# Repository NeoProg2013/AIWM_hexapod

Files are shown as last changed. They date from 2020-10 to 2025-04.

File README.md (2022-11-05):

# AIWM hexapod (Artificial intelligence walking machine)



## Цикл статей по разработке:

* https://habr.com/ru/post/424867/ – проектирование
* https://habr.com/ru/post/424905/ – сборка
* https://habr.com/ru/post/436748/ – кинематика
* https://habr.com/ru/post/444070/ – ядро передвижения
* https://habr.com/ru/post/448058/ – электроника
* https://habr.com/ru/post/478812/ – проектирование для 3D печати
* https://habr.com/ru/post/111111/ – пластиковый корпус и прикладное ПО
* https://habr.com/ru/post/493304/ – улучшенная математика передвижения
* https://habr.com/ru/post/507762/ – завершение версии 1.00
* https://habr.com/ru/post/543620/ – датчики касания
* https://habr.com/ru/post/567034/ – стабилизация
* https://habr.com/ru/company/ruvds/blog/648019/ – новое ядро передвижения

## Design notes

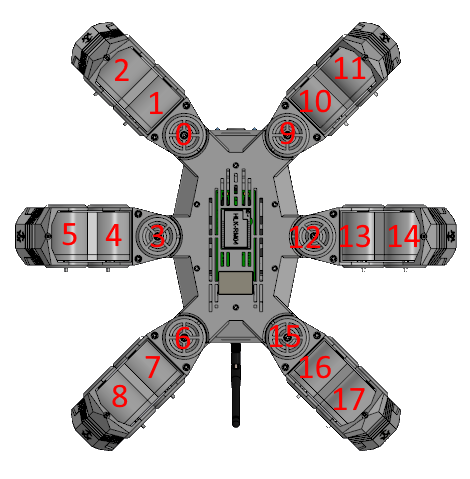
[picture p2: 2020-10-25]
docs/Servo numbering.png

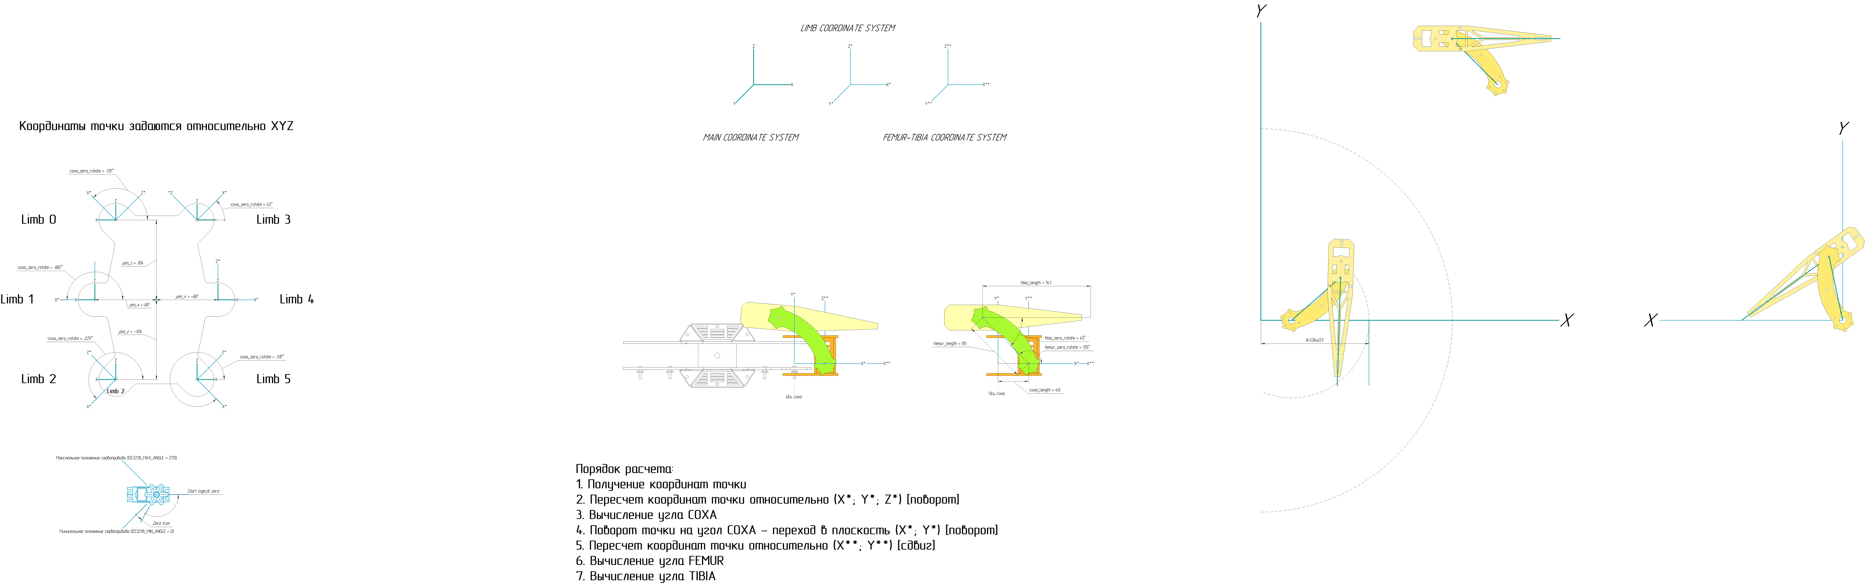
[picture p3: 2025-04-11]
docs/Сoordinate system.png

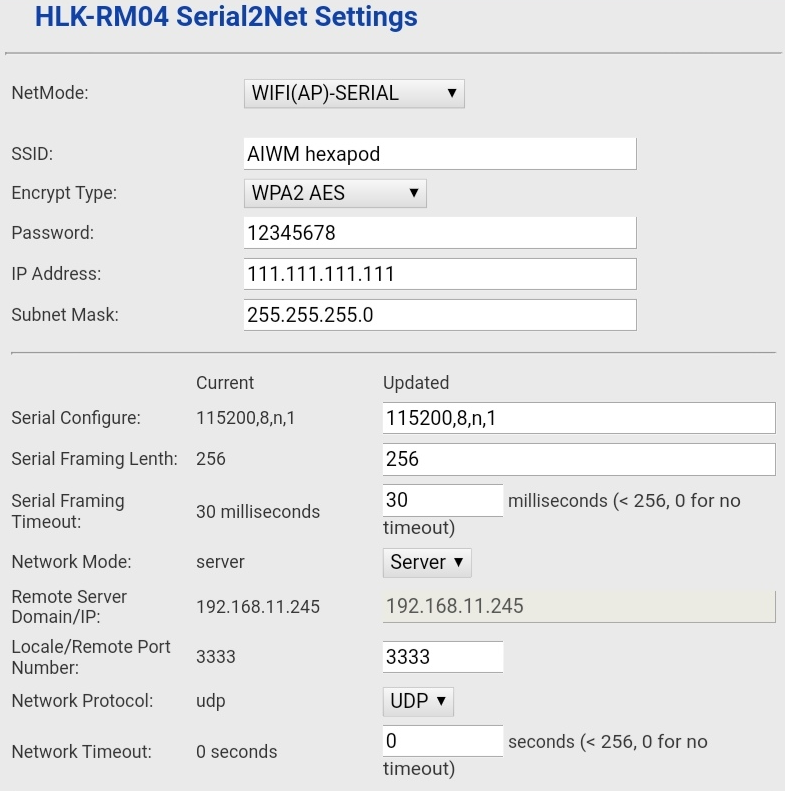
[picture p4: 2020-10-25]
docs/HLK-RM04 cfg.png

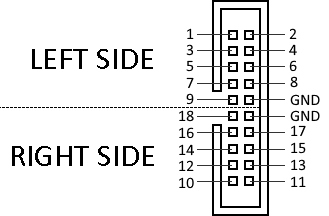
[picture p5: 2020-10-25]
docs/Servo connector pin map.png

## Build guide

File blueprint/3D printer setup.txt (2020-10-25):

Основа 1.1: 
 - Высота слоя: 0.2
 - Высота первого слоя: 0.2
 - Толщина стенки: 0.8
 - Слои дна\крышки: 2\3
 - Заполнение: 10%
 
Основа 1.2: 
 - Высота слоя: 0.2
 - Высота первого слоя: 0.2
 - Толщина стенки: 0.8
 - Слои дна\крышки: 2\3
 - Заполнение: 10%
 
Основа 1.3: 
 - Высота слоя: 0.2
 - Высота первого слоя: 0.2
 - Толщина стенки: 0.8
 - Слои дна\крышки: 3\2
 - Заполнение: 10%
 
Основа 1.4: 
 - Высота слоя: 0.2
 - Высота первого слоя: 0.2
 - Толщина стенки: 0.8
 - Слои дна\крышки: 3\2
 - Заполнение: 10%
 
Основа 1.5: 
 - Высота слоя: 0.2
 - Высота первого слоя: 0.2
 - Толщина стенки: 0.8
 - Слои дна\крышки: 3\2
 - Заполнение: 10%
 
Крышки верхняя и нижняя: 
 - Высота слоя: 0.2
 - Высота первого слоя: 0.2
 - Толщина стенки: 0.8
 - Слои дна\крышки: 3\2
 - Заполнение: 5%

Опора 3: 
 - Высота слоя: 0.2
 - Высота первого слоя: 0.1
 - Толщина стенки: 0.8
 - Слои дна\крышки: 2\3
 - Заполнение: 10%

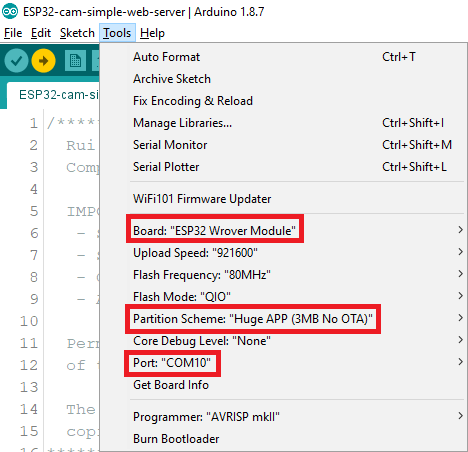
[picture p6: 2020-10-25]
firmware/ESP32-CAM/Arduino IDE setup.png

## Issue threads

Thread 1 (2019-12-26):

[v1.00 - blueprint] Add clearance between vertical slider connectors on body

NeoProgAIM, 2019-12-26:
Need add clearance between vertical slider connectors on body

NeoProgAIM, 2019-12-26:
Done c158953. Decreased height of parts on figure by 0.5mm.

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

Closed 2019-12-26.

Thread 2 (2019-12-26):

[v1.00] Печать и сборка прототипа корпуса

NeoProg2013, 2019-12-26:
Задача по печати корпуса. Это сообщение будет периодически обновляться в время печати и показывать прогресс и время печати каждой детали.

| Part name 	| Print time (x1) 	|  Progress 	|  % 		|  Status		|  Weight (g)	|
| ---- 		|:----:			|:----:		|:----:	|  :----:		|  :----:		|
| Base_1_1	| 4:00 			| 1\1  		| 100% 	|  Done		| ? 			|
| Base_1_2	| 4:10 			| 1\1  		| 100% 	|  Done		| ? 			|
| Base_1_3	| 8:40 			| 1\1  		| 100% 	|  Done		| ? 			|
| Base_1_4	| 2:20 			| 2\2  		| 100% 	|  Done		| ? 			|
| Base_1_5	| 3:20 			| 1\1  		| 100% 	|  Done		| ? 			|
| Top_cap		| 2:20 			| 1\1  		| 100% 	|  Done		| ? 			|
| Bot_cap		| 2:30 			| 1\1  		| 100% 	|  Done		| ? 			|
| Batt_cap	| 0:20 			| 1\1  		| 100% 	|  Done		| ? 			|
| Limb_1_1	| 1:40 			| 6\6  		| 100%	|  Done		| 36	 		|
| Limb_1_2	| 0:30 			| 6\6  		| 100% 	|  Done		| 5 			|
| Limb_1_3	| 0:30 			| 6\6  		| 100% 	|  Done		| 4 			|
| Limb_2_1	| 2:55 			| 6\6  		| 100% 	|  Done		| 53 			|
| Limb_2_2	| 1:00 			| 6\6  		| 100%	|  Done		| 12 			|
| Limb_3_1	| 2:33 			| 6\6  		| 100% 	|  Done		| 45 			|
| Limb_3_2	| 2:33 			| 3\3  		| 100% 	|  Done		| 30			|
| Limb_3_2_M	| 2:33 			| 3\3  		| 100%	|  Done		| 30 			|

M - деталь отражена зеркально

Вес центральной части (без приводов): 460g
Суммарный вес конечностей (без приводов): 1110g
Суммарный вес приводов: 1230g
Суммарный вес корпуса: 460 + 1110 + 1230 = 2800g

NeoProgAIM, 2019-12-26:
Parts Base_1_1, Base_1_3 and Base_1_4 printing is completed after fix founded bugs:
1. Absent clearance between Base_1_1 and Base_1_3. Vertical slider is stuck.
2. Absent clearance between Base _1_1 and bottom part of Base_1_3. Vertical connectors on Base_1_3 is protrude.

NeoProgAIM, 2020-01-21:
Сборка корпуса закончена. Больше косяков не обнаружено

Closed 2020-03-21.

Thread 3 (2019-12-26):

[v1.00 - blueprint] Need decrease holes depth for "IMBUS" screw

NeoProgAIM, 2019-12-26:
Need decrease holes depth for "IMBUS" screw. Probably 1mm will be sufficient.

NeoProgAIM, 2019-12-26:
Done 34bbd21. This bug detected only for Base_1_1, now it is fixed

Closed 2019-12-26.

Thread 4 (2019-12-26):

[v1.00 - blueprint] Add holes for wire from foot sensors

NeoProgAIM, 2019-12-26:
Need add holes for wire from foot sensors

NeoProgAIM, 2019-12-26:
Not actual. Wires will be enter to hull together with wires from servo motors

Closed 2019-12-26.

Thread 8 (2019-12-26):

[v1.00 - hardware] Produce and running control board prototype

NeoProgAIM, 2019-12-26:
Task for running control board prototype. This task will be periodically update for show founded bugs

NeoProgAIM, 2020-01-05:
PCB version 4d56e51 already send for produce

NeoProgAIM, 2020-01-16:
Binding timers to PWM outputs:
- Main sync: TIM2 (32-bit)
- Limb_1_1: TIM3 CH1 (16-bit)
- Limb_1_2: TIM3 CH2 (16-bit)
- Limb_1_3: TIM3 CH3 (16-bit)
- Limb_2_1: TIM3 CH4 (16-bit)
- Limb_2_2: TIM4 CH1 (16-bit)
- Limb_2_3: TIM4 CH2 (16-bit)
- Limb_3_1: TIM4 CH3 (16-bit)
- Limb_3_2: TIM4 CH4 (16-bit)
- Limb_3_3: TIM12 CH1 (16-bit)
- Limb_4_1: TIM12 CH2 (16-bit)
- Limb_4_2: TIM13 CH1 (16-bit)
- Limb_4_3: TIM13 CH2 (16-bit)
- Limb_5_1: TIM14 CH1 (16-bit)
- Limb_5_2: TIM14 CH2 (16-bit)
- Limb_5_3: TIM15 CH1 (16-bit)
- Limb_6_1: TIM15 CH2 (16-bit)
- Limb_6_2: TIM16 CH1 (16-bit)
- Limb_6_3: TIM16 CH2 (16-bit)

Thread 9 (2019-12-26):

[v1.00 - firmware] - Buzzer driver

NeoProgAIM, 2019-12-26:
Need porting or rewrite buzzer driver

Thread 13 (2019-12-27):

[v1.00 - hardware] Check possible replace STM32F373 on STM32F303

NeoProgAIM, 2019-12-27:
Need check possible replace STM32F373 on STM32F303. Demo board for STM32F373 have very big price, but STM32F303 have low price. It is need for start firmware porting procedure during producing of control board

NeoProgAIM, 2019-12-27:
No. Minimum order for STM32F303 be 25 pieces.

Closed 2019-12-27.

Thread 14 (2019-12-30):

[v1.00] Need redesign Limb_1

NeoProgAIM, 2019-12-30:
3D printer cannot printing Limb_1 with good quality. Need redesign it with separate parts. Also bearing now useless because nut stuck to bottom side of Limb_1 and it can`t rotate

NeoProgAIM, 2020-01-01:
Redesign completed in ec0b346. Also descreased clearance between limb nodes to 1.5mm

Closed 2020-01-01.

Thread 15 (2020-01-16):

[v1.00] Улучшение расчетов обратной кинематики

NeoProg2013, 2020-01-16:
Можно упростить алгоритм расчета угла COXA. Можно удалить одну операцию поворота и заменить расчет на:

> COXA = coxa_zero_rotate - (atan2(z, x) * 180 / PI)
Где Z и X - координаты точки назначения

Необходимо реализовать и проверить это

NeoProg2013, 2021-08-15:
Вошло в релиз 1.01

Closed 2021-08-15.

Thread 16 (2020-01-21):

[v1.00] Изменить тип переменной synchro на uint64_t

NeoProgAIM, 2020-01-21:
Необходимо изменить тип переменной synchro на uint64_t для исключения ситуации переполнения счетчика.

NeoProgAIM, 2020-02-04:
Реализовано в f61455d621782df915f37f17892af658224689de при портировании драйвера

Closed 2020-02-04.

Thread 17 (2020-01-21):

[v1.00] Необходимо сделать вырез для оси сервопривода в Limb_1_3 и Limb_3

NeoProgAIM, 2020-01-21:
Необходимо сделать вырез для оси сервопривода в Limb_1_3 и Limb_3. Сейчас данная часть надевается только раздвинуть крепления. Это усложняет сборку

NeoProgAIM, 2020-02-04:
Реализовано. Перепечатывать элементы пока не планируется

Closed 2020-02-04.

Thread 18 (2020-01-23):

[v1.00] Добавить вырез под провода от сервоприводов в Limb_2_2

NeoProgAIM, 2020-01-23:
Необходимо добавить вырез под провода от сервоприводов в Limb_2_2, так как при текущей реализации провода оказываются слишком короткими

NeoProgAIM, 2020-02-04:
Реализовано в 1ae15879f8d5a6824e3ce302d24f2b5777b99fb4

Closed 2020-02-04.

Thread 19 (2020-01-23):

[v1.00] Переход на прямое питание от АКБ

NeoProgAIM, 2020-01-23:
Необходимо перейти на прямое питание от 2S АКБ. Была проверена работа DS3218MG от 8.4В - приводы работали.

Нужно провести нагрузочные тесты и оценить нагрев электроники и привода

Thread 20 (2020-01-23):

[v1.00] Переход на прямое питание от АКБ

NeoProgAIM, 2020-01-23:
Необходимо перейти на прямое питание от 2S Li-Po АКБ.

В рамках задачи нужно провести нагрузочные тесты приводов при прямом питании от АКБ и оценить нагрев DC мотора и электроники. Возможно понадобится сделать вырезы для охлаждения приводов и вентиляции корпуса.

Так же нужно будет спроектировать простую плату-адаптер для распределения питания по приводам.

NeoProgAIM, 2020-01-24:
Плохая идея. Под нагрузкой транзисторы на плате управления приводом очень сильно нагреваются. Питаться от АКБ не вариант - нужен DC-DC

Closed 2020-01-24.

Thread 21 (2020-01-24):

[v1.00] Develop notes

NeoProgAIM, 2020-01-24:
В этом сообщении будет фиксироваться история разработки и совершенные ошибки:
1. Сборка корпуса завершена
2. Изменен и протестирован драйвер сервоприводов
3. Создана конфигурация приводов для текущей версии

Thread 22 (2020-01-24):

[v1.00] Добавить в конфигурацию мин. и макс. значения угла привода

NeoProgAIM, 2020-01-24:
Нужно добавить в конфигурацию мин. и макс. значения угла привода для защиты приводов от смерти. В результате экспериментов был убит один из приводов и теперь введение данной функциональности очень актуально.

Планируется ограничение физического угла

NeoProgAIM, 2020-02-04:
Добавлены необходимые переменные в логику работы драйвера сервопривода (на данный момент код находится в приватном репозитории)

Closed 2020-02-04.

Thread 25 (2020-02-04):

[v1.00] Запуск новой платы управления и перенос прошивки на новый МК

NeoProg2013, 2020-02-04:
Задача по запуску новой платы управления и переносу прошивки на новый контроллер. Это сообщение будет периодически обновляться по мере прогресса:

### Процесс:
1. Запущена отладка и залита пустое FW в контроллер
2. Реализована настройка тактирования МК
3. Запущен модуль SYSTIMER
4. Завершен перенос модуля PWM
5. Завершен перенос модуля USART
6. Завершен перенос модуля ADC
7. Завершен перенос модуля I2C
8. Завершен перенос модулей CLI, COMMINICATION и SWP
9. Завершен перенос модулей SYSMON и CONFIGURATOR
10. **Завершен перенос необходимой базы для начала портирования основной логики**
11. Завершен перенос модуля SERVO_DRIVER
12. Проверена работоспособность схемы управления LED
13. Частично перенесен драйвер конечностей
14. Перенесен движок передвижения
15. **Плата полностью протестирована**
16. Реализован модуль управления LED и пьезопещалкой
17. Настроены последовательности под новый корпус

### Ошибки в процессе работы и комментарии по улучшению:
* Впаял вместо диода для защиты от переполюсовки перемычку - зря. Как итог спалил регулятор на 3.3В. Временно заменен на LM1117
* Добавлены названия для тестовых точек на плате (silk layer)
* Добавлен указатель на плюсовой пин разъема питания (silk layer)
* **Необходимо увеличить heat sink на нижнем слое для 5V стабилизатора**
* Увеличена высота верхней крышки на 2мм

Closed 2020-04-25.

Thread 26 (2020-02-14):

[v1.00] Делитель напряжения в затворе транзисторов

NeoProg2013, 2020-02-14:
Необходимо убрать делитель напряжения в затворе транзисторов для LEDs и Buzzer

NeoProg2013, 2020-02-17:
Исправлено в aa0dc20162d15389f73c5938317842dc2906b525

Closed 2020-02-17.

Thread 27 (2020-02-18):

[v1.00] Оптимизация драйвера ШИМ

NeoProg2013, 2020-02-18:
Драйвер оптимизирован 8fc3e4fe0a1396290fbbdc6e70567ce44be115d4

Результаты
|  							| До 	| После (FLASH)	| После (RAM)	|
| :----:						|:----: 	|:----:			|:----:		|
| Подготовка нового периода	| 67.67us 	| 43us			| 48us		|

Closed 2020-02-18.

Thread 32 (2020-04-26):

[v1.00] Обновление платы управления (CAM)

NeoProg2013, 2020-04-26:
Новая плата управления должна поддерживать следующие возможности:
* Коммуникация по WIFI (SWLP)
* ~~Управление питанием ESP32-CAM~~
* ~~Отдельное питание для ESP32-CAM~~
* Питание ESP32-CAM от 3V3 и подключение к USART
* Управление питанием приводов ~~через реле~~ пин EN на каждом канале DC-DC
* Прошивка через FTDI
* Проводной CLI через FTDI
* Управление RGB светодиодами (есть возможность регулировать яркость подстроечными резисторами)
* Управление пищалкой
* Возможность подключения дисплея I2C
* Возможность подключения концевиков
* Добавлена возможность управления сверхярким передним светодиодом (схема управления на плате питания)

NeoProg2013, 2020-06-01:
bbdf743
Плата отдана в производство

NeoProg2013, 2020-06-23:
Плата заказана и уже в пути bbdf743

Closed 2020-08-30.

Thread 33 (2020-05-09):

[v1.00] Обновление платы питания (LM2678)

NeoProg2013, 2020-05-09:
Необходимо проверить новый DC-DC на базе LM2678:
* Пиковый ток должен достигать 8А
* Продолжительная работа при 5А (возможен внешний обдув)
* Оценить нагрев PCB и её элементов
* Оценить пульсации выходного напряжения

NeoProg2013, 2020-05-09:
LM2678_prototype - ветка для разработки прототипа

NeoProg2013, 2020-06-01:
bbdf743
Плата отдана в производство.

NeoProg2013, 2020-06-23:
Плата заказана и уже в пути bbdf743

NeoProg2013, 2020-08-30:
Добавлены керамические конденсаторы на 2 и 4 ноги LM. Припаяны прям на ноги.

Closed 2020-08-30.

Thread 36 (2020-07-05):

[v1.00] Перенос zero_trim в другую часть выражения

NeoProg2013, 2020-07-05:
Нужно рассмотреть возможность переноса переменной zero_trim в левую часть выражения. Т.е.
`(float)(config->logic_zero + config->zero_trim) - logic_angle`

Оригинал:
```
if (config->config & MM_SERVO_CONFIG_REVERSE_DIRECTION_MASK) {
    physic_angle = (float)config->logic_zero - (logic_angle + (float)config->zero_trim);
}
else {
    physic_angle = (float)config->logic_zero + (logic_angle + (float)config->zero_trim);
}
```

NeoProg2013, 2020-07-08:
Появляется зависимость от направления сервопривода. Отклонено

Closed 2020-07-08.

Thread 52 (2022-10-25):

Добавить положение центра coxa относительно центра корпуса в параметры конечности

NeoProg2013, 2022-10-25:
float z_sign = 1.0f;
if (limbs[i].pos.z) {
	z_sign = limbs[i].pos.z / fabs(limbs[i].pos.z);
}
float z = limbs[i].pos.z + z_sign * 104.0f; // 104 - coxa position from center by axix Z

float x_sign = 1.0f;
if (limbs[i].pos.x) {
	x_sign = limbs[i].pos.x / fabs(limbs[i].pos.x);
}
float x = limbs[i].pos.x + x_sign * 104.0f;

Нужно избавиться от констант в коде, особенно учитывая, что вот тут
`float x = limbs[i].pos.x + x_sign * 104.0f;`
она неверная

NeoProg2013, 2022-12-18:
Добавлено в fb7326425be7602cb75545adbe0825031f6e9c19

Closed 2022-12-18.

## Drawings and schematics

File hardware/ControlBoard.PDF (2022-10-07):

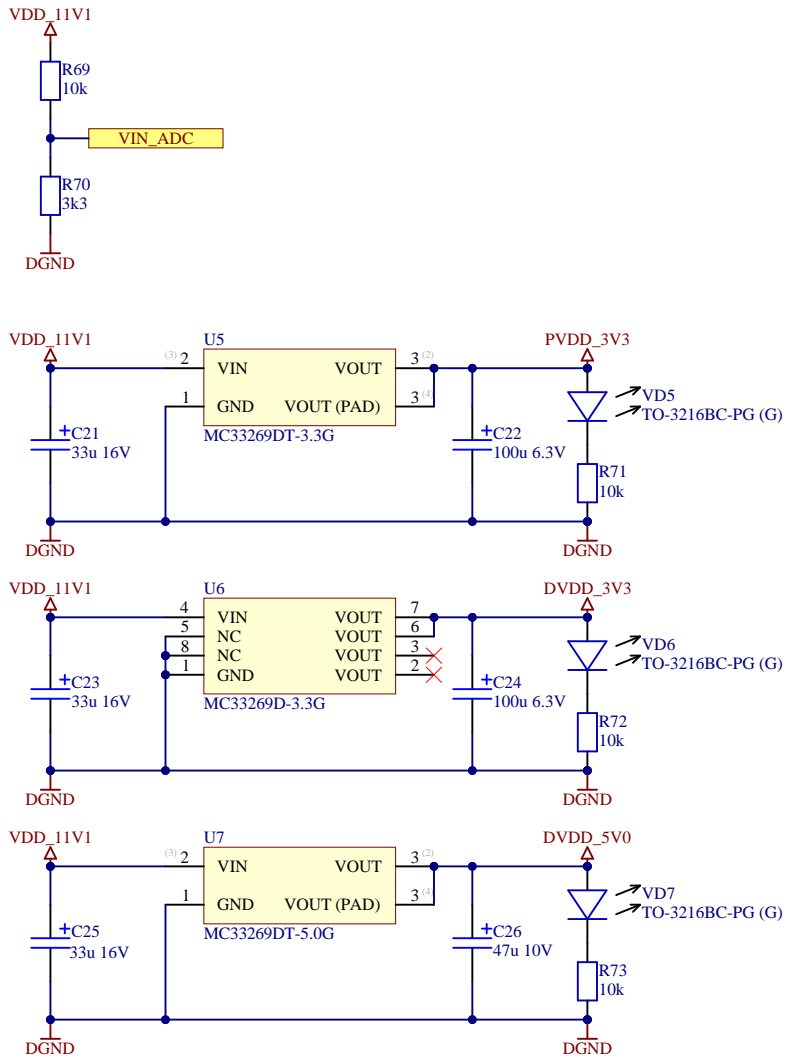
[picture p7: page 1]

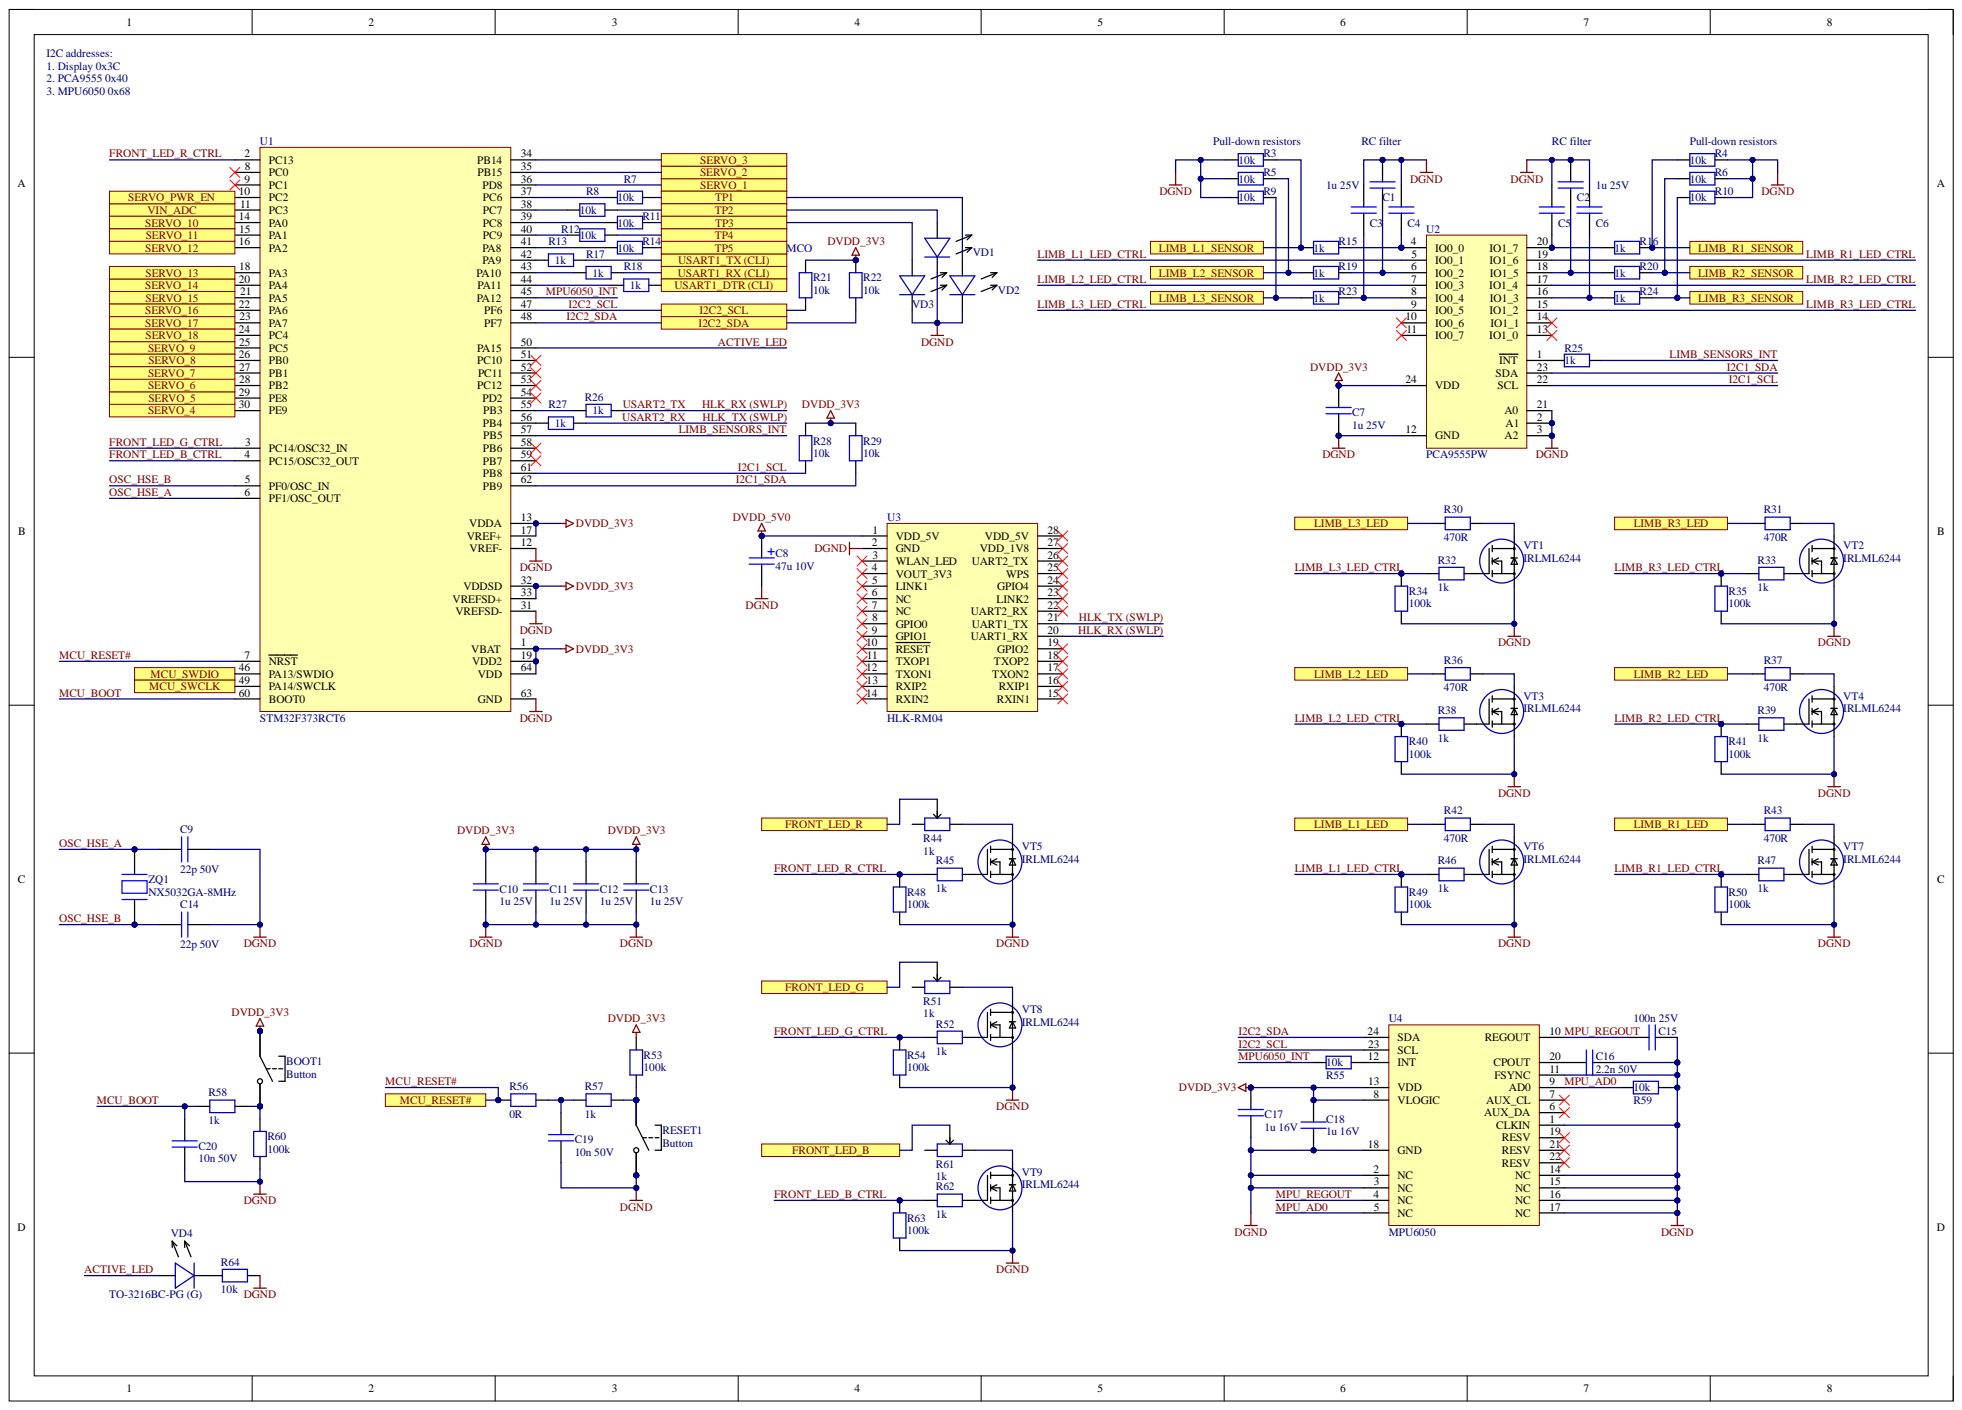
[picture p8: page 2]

VIN_ADC | | PC3 11 | TP2

PA1 15 | | DVDD_3V3 MCO

SERVO_18 | | ACTIVE_LED
SERVO_9 | PC5 25

SERVO_7 | PB2 28

MPU_AD0 | 10k

MCU_RESET# | GND 18 | R59

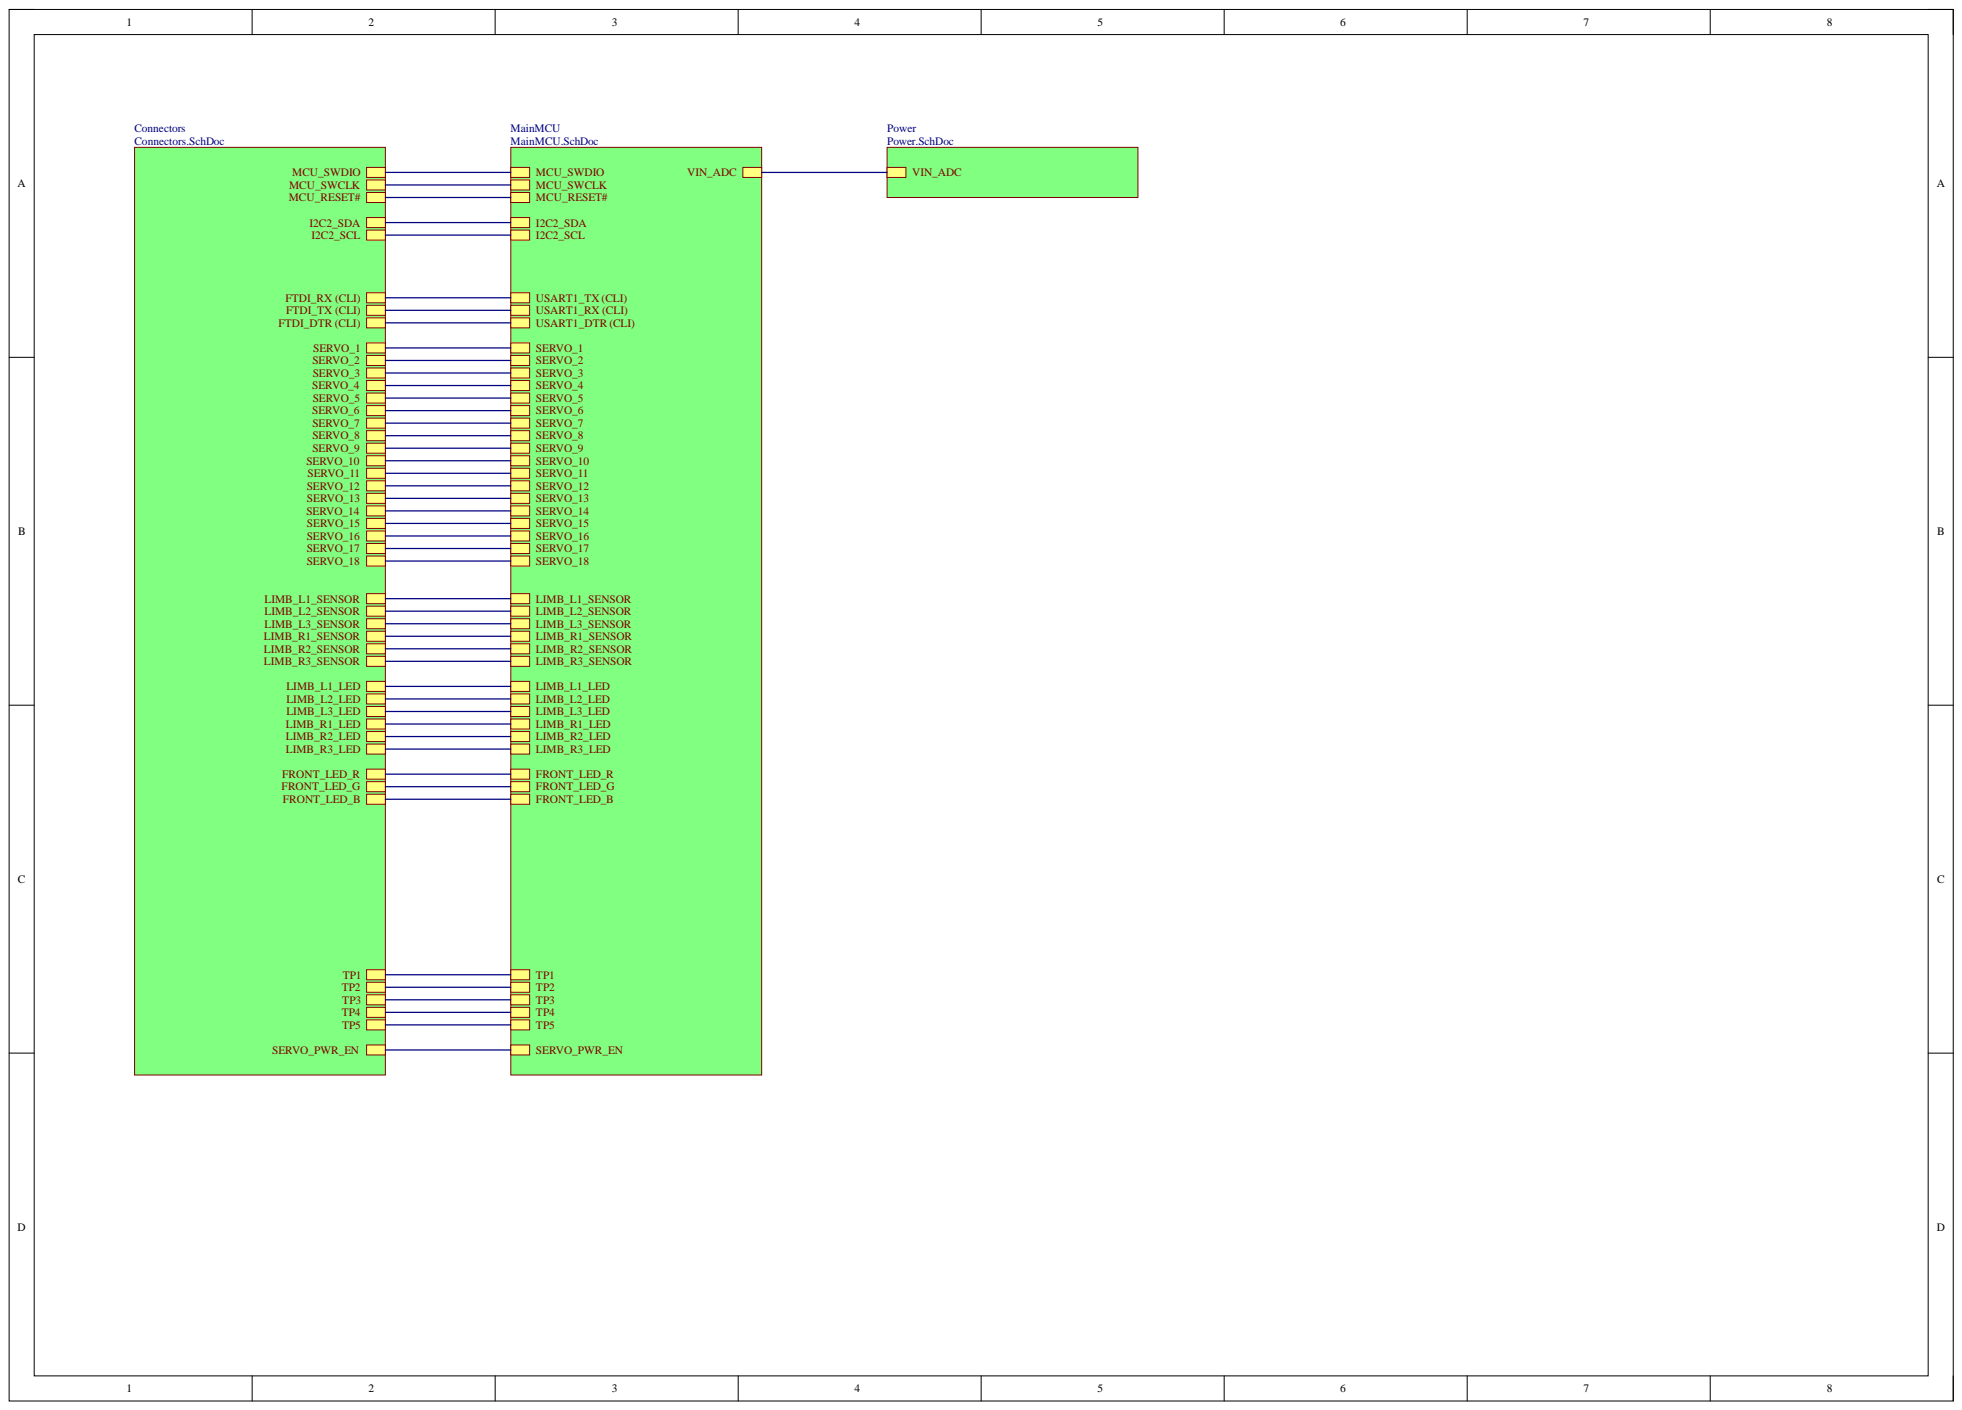
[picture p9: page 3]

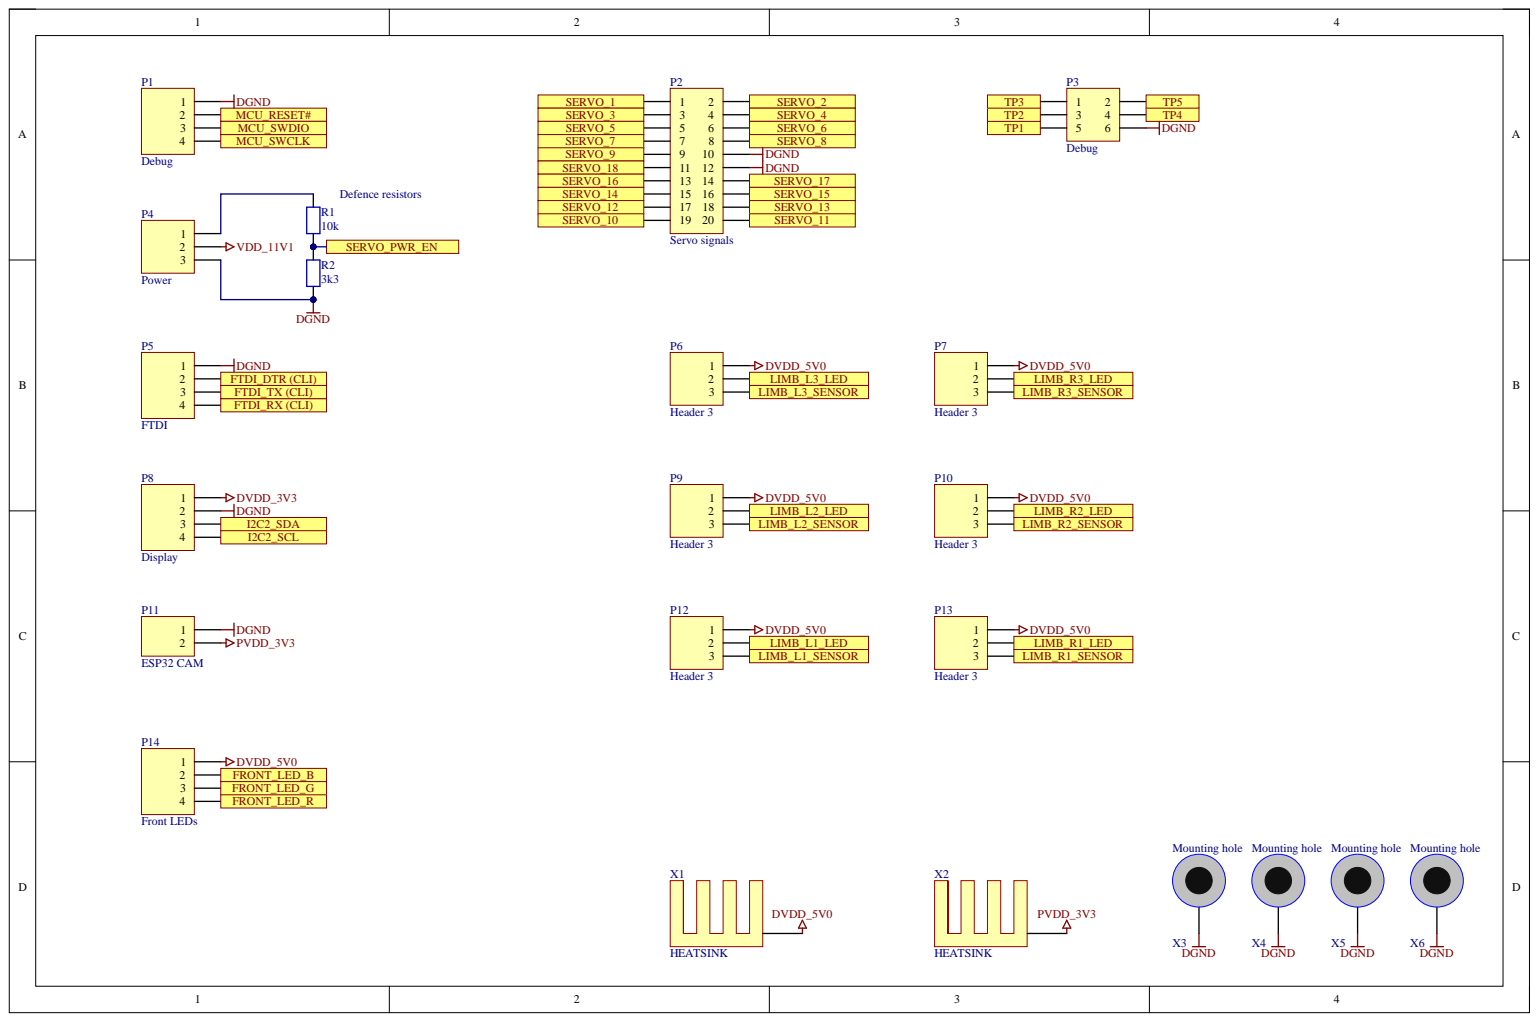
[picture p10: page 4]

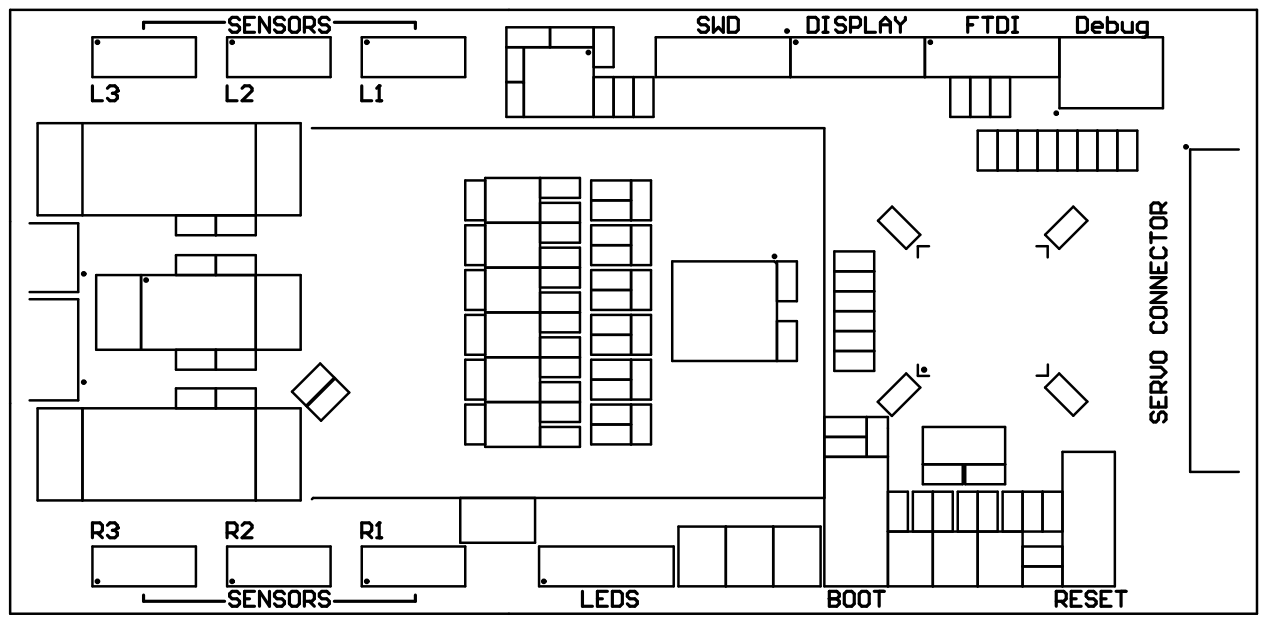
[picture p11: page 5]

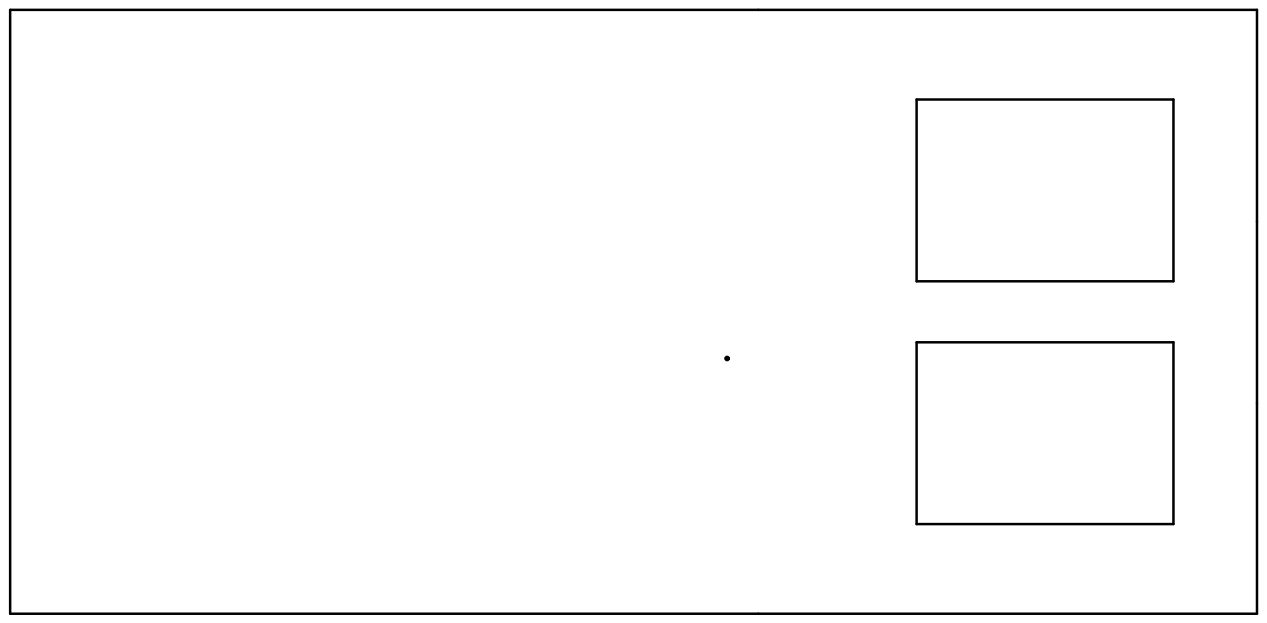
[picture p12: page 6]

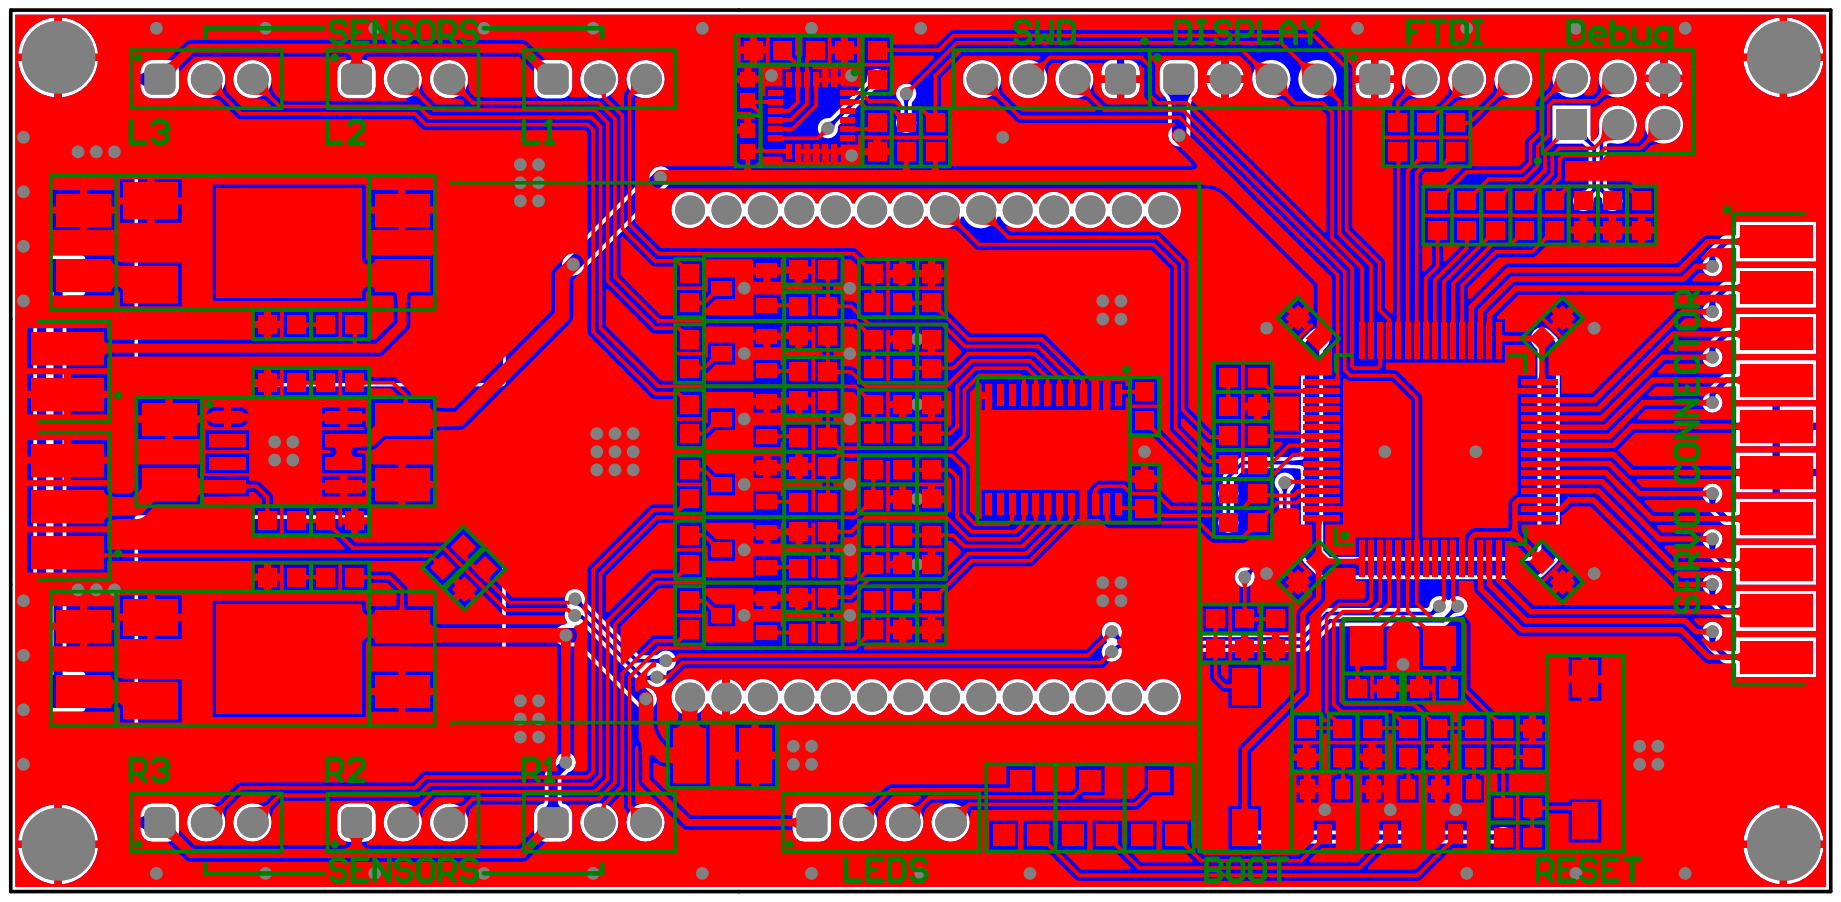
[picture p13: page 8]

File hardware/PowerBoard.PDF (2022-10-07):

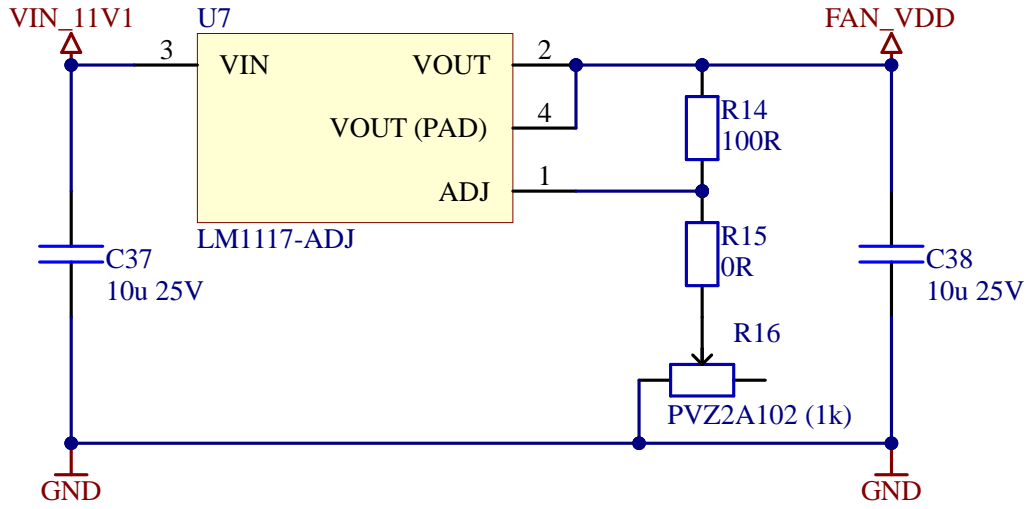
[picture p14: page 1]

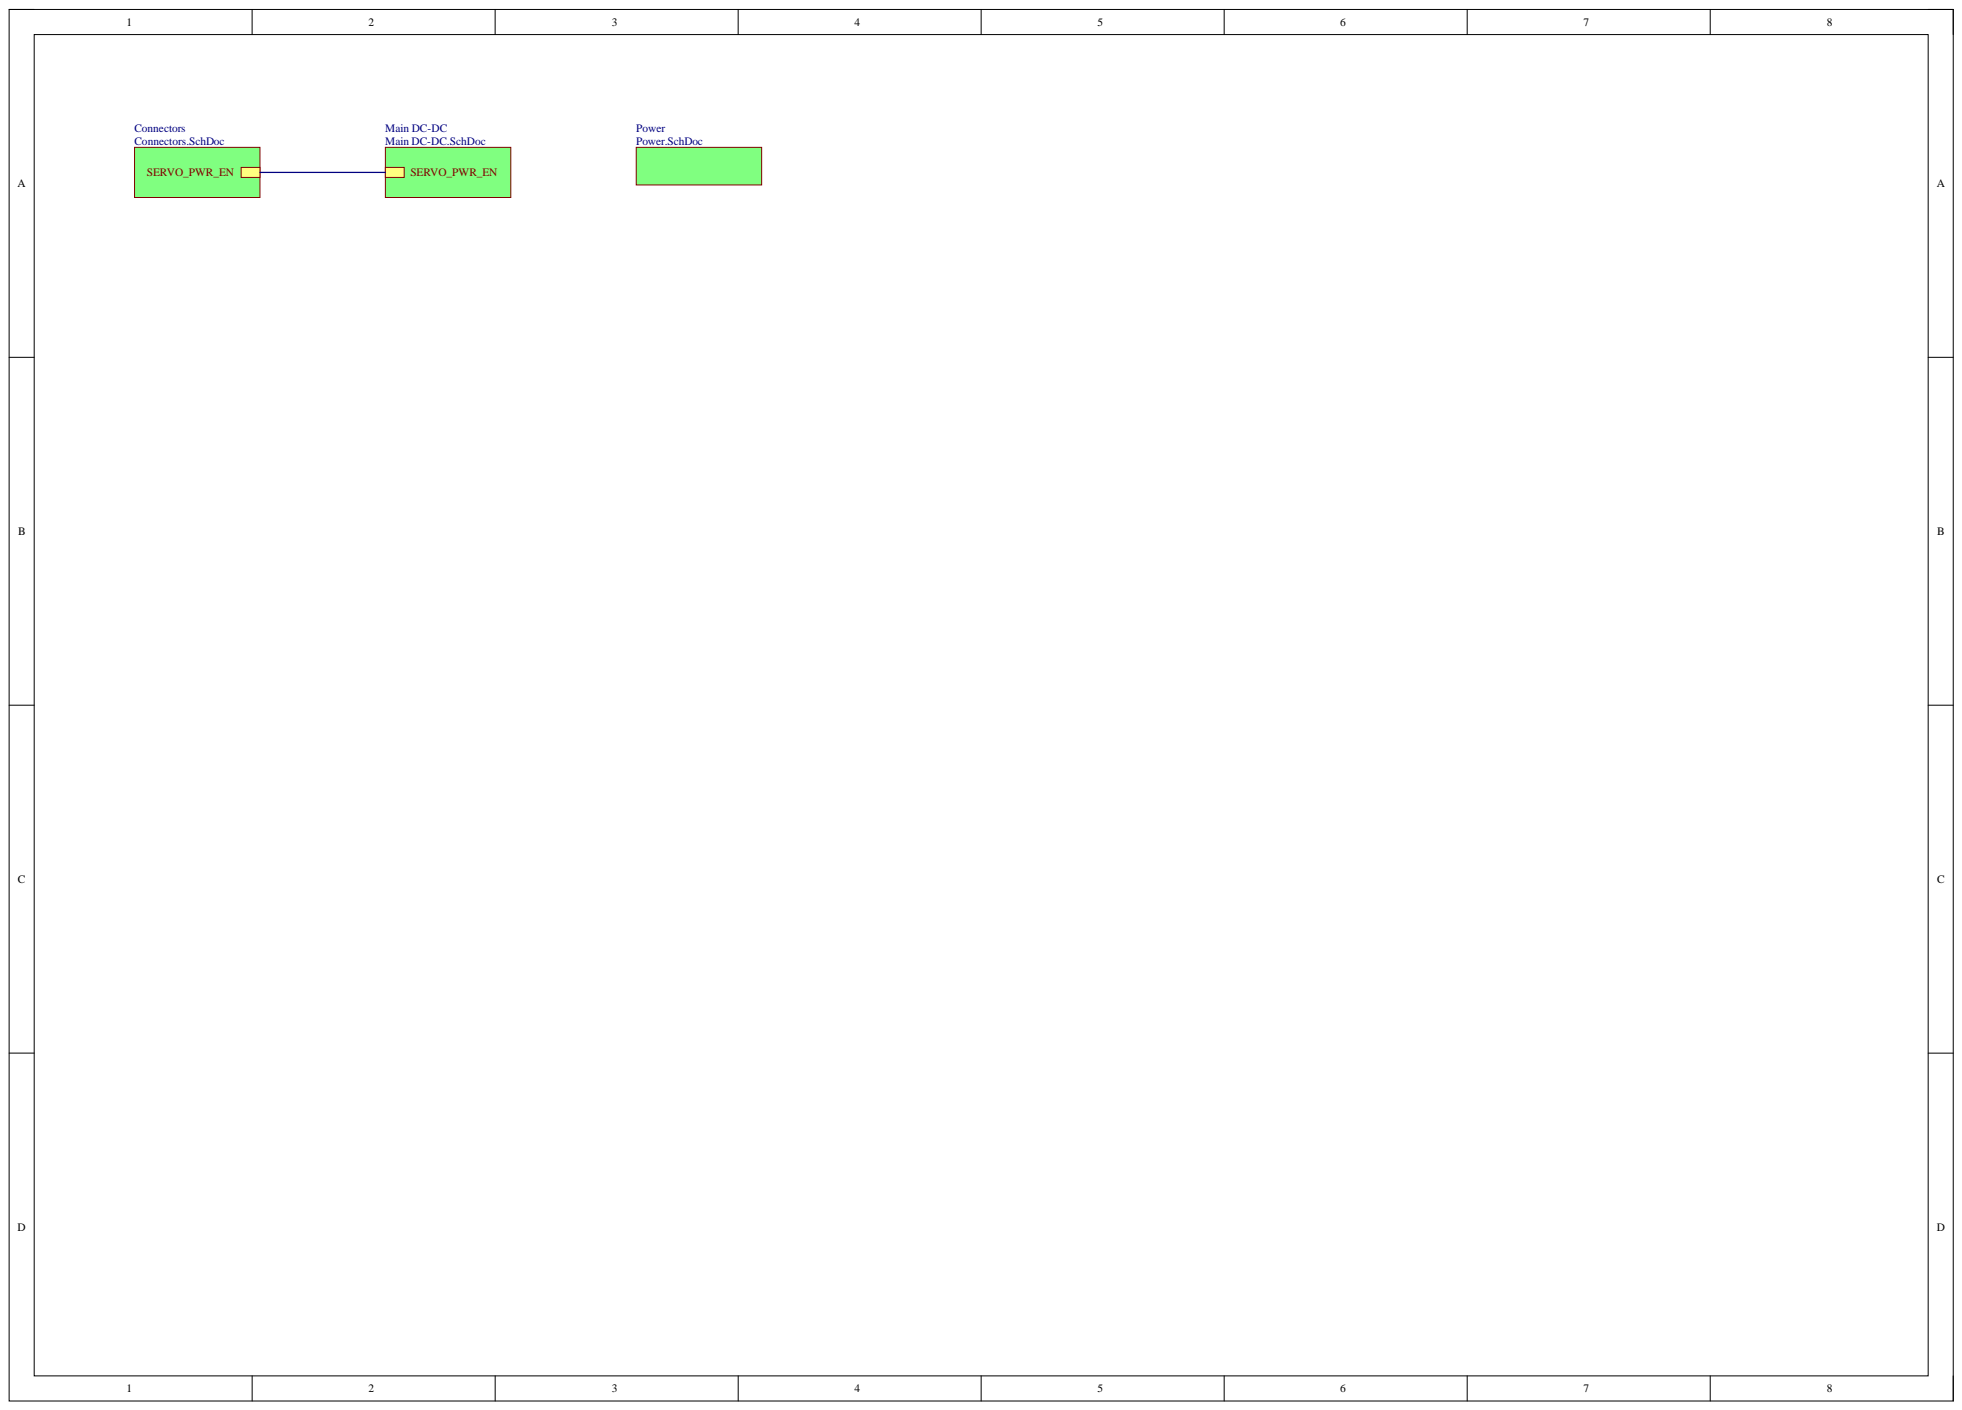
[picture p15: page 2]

Main DC-DC
Main DC-DC.SchDoc

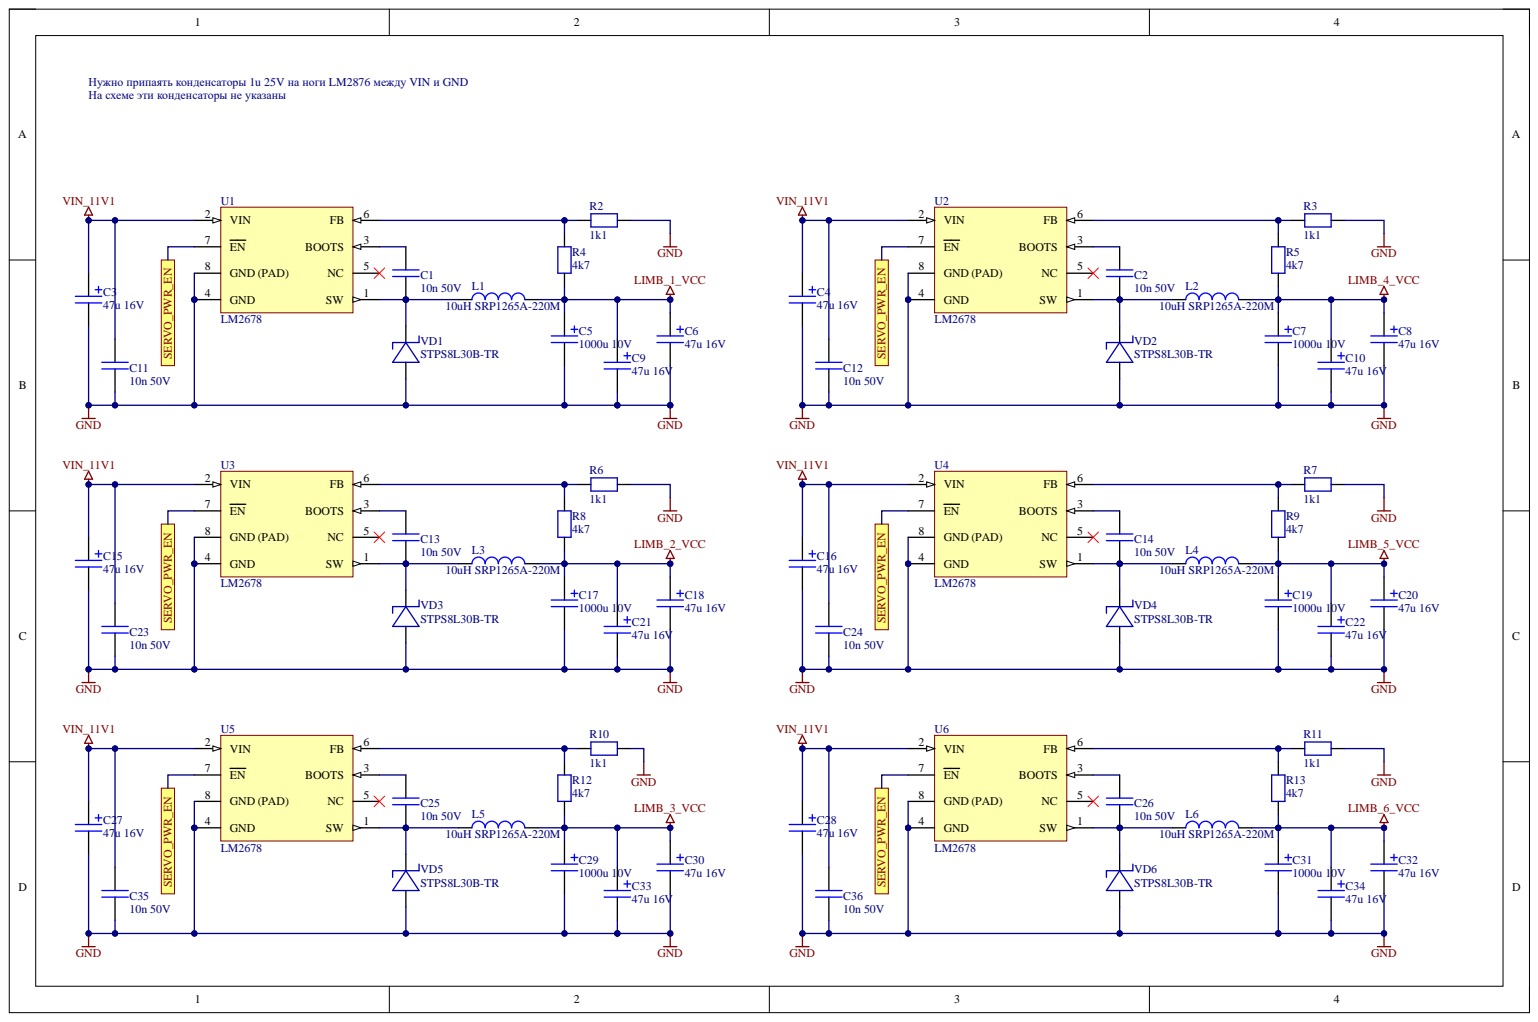
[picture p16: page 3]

Нужно припаять конденсаторы 1u 25V на ноги LM2876 между VIN и GND
На схеме эти конденсаторы не указаны

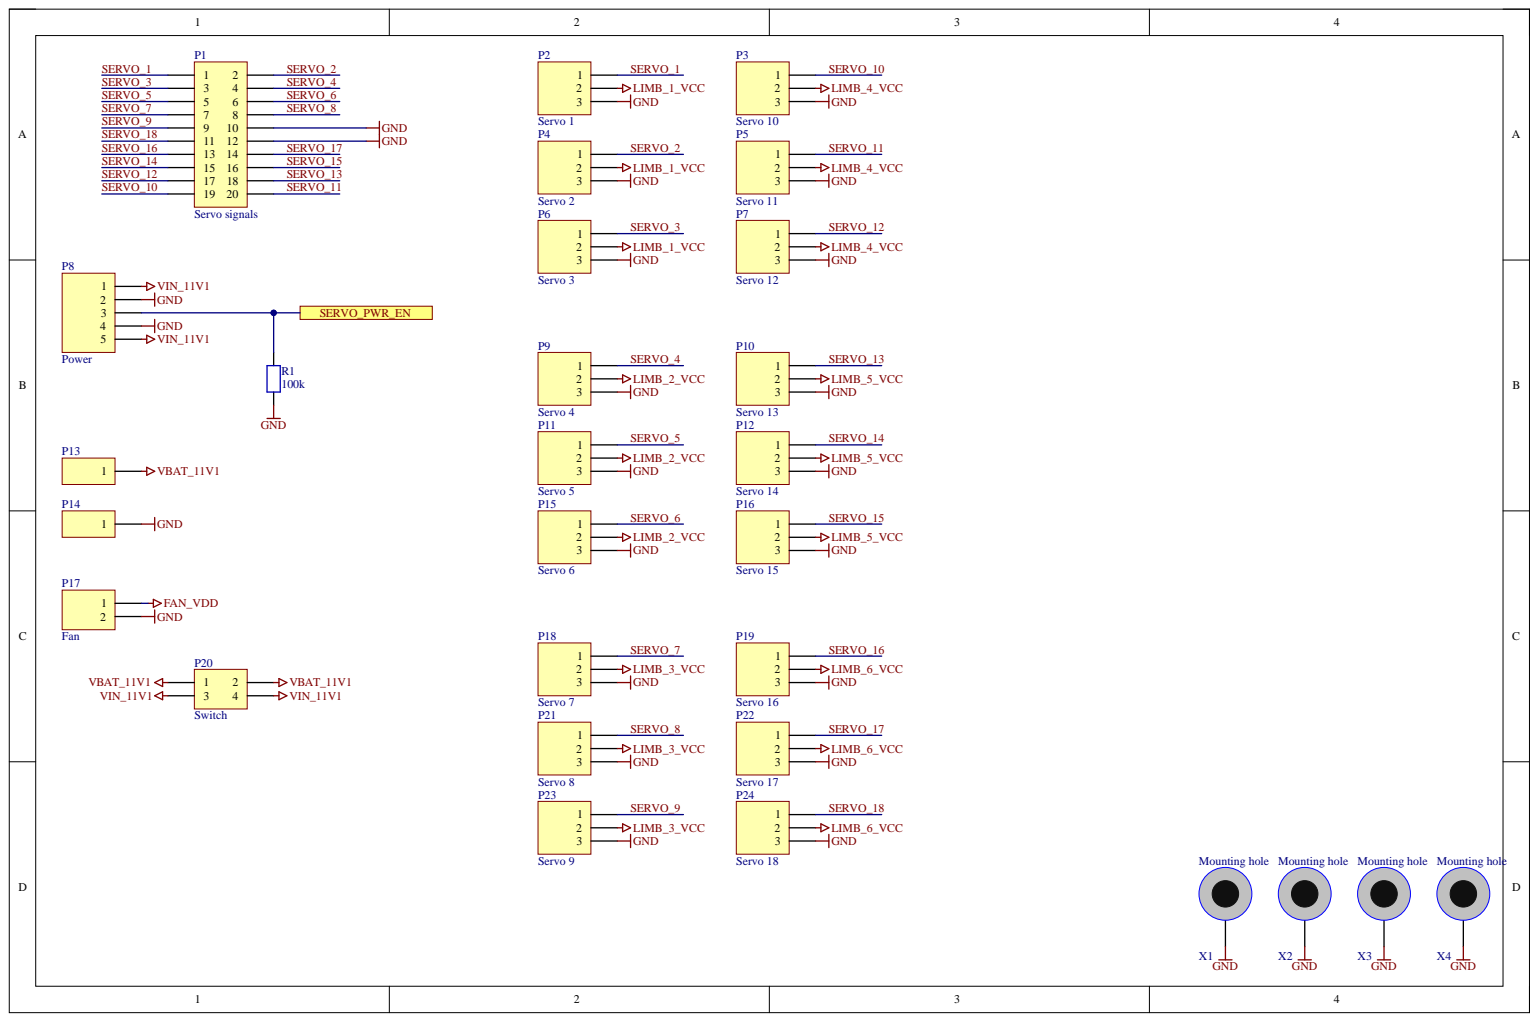
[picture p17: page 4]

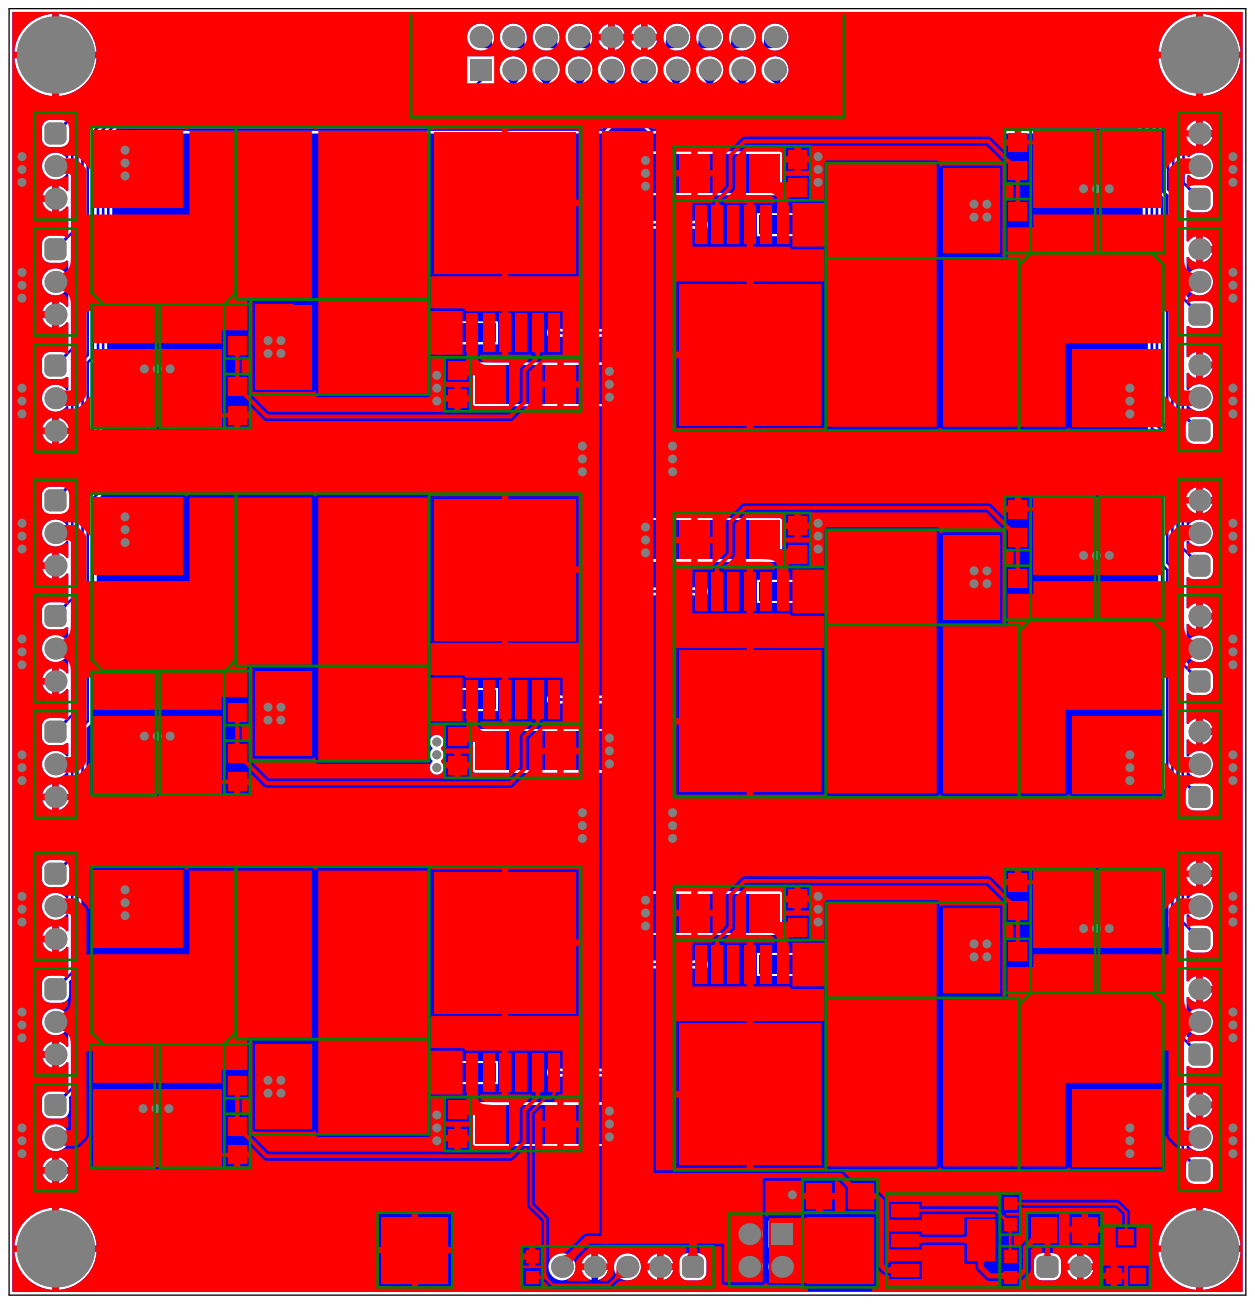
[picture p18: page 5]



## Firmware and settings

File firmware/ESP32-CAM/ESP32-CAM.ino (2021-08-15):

#include "esp_camera.h"
#include "WiFi.h"
#include "esp_timer.h"
#include "img_converters.h"
#include "Arduino.h"
#include "fb_gfx.h"
#include "soc/soc.h"
#include "soc/rtc_cntl_reg.h"
#include "esp_http_server.h"
 
// WiFi setup
const char* ssid = "AIWM hexapod";
const char* password = "12345678";
 
#define PART_BOUNDARY "123456789000000000000987654321"
 
#define PWDN_GPIO_NUM     32
#define RESET_GPIO_NUM    -1
#define XCLK_GPIO_NUM      0
#define SIOD_GPIO_NUM     26
#define SIOC_GPIO_NUM     27
#define Y9_GPIO_NUM       35
#define Y8_GPIO_NUM       34
#define Y7_GPIO_NUM       39
#define Y6_GPIO_NUM       36
#define Y5_GPIO_NUM       21
#define Y4_GPIO_NUM       19
#define Y3_GPIO_NUM       18
#define Y2_GPIO_NUM        5
#define VSYNC_GPIO_NUM    25
#define HREF_GPIO_NUM     23
#define PCLK_GPIO_NUM     22
 
static const char* _STREAM_CONTENT_TYPE = "multipart/x-mixed-replace;boundary=" PART_BOUNDARY;
static const char* _STREAM_BOUNDARY = "\r\n--" PART_BOUNDARY "\r\n";
static const char* _STREAM_PART = "Content-Type: image/jpeg\r\nContent-Length: %u\r\n\r\n";
 
httpd_handle_t stream_httpd = NULL;
 
static esp_err_t stream_handler(httpd_req_t* req) {
    
    size_t _jpg_buf_len = 0;
    uint8_t* _jpg_buf = NULL;
    char* part_buf[64];
    
    esp_err_t res = httpd_resp_set_type(req, _STREAM_CONTENT_TYPE);
    if(res != ESP_OK) {
        return res;
    }
    
    while(true){
        
        camera_fb_t* fb = esp_camera_fb_get();
        if (!fb) {
            Serial.println("ERROR");
            res = ESP_FAIL;
        } 
        else {
            if (fb->format != PIXFORMAT_JPEG){
                bool jpeg_converted = frame2jpg(fb, 80, &_jpg_buf, &_jpg_buf_len);
                esp_camera_fb_return(fb);
                fb = NULL;
                if (!jpeg_converted) {
                    Serial.println("ERROR");
                    res = ESP_FAIL;
                }
            } 
            else {
                _jpg_buf_len = fb->len;
                _jpg_buf = fb->buf;
            }
        }
        if (res == ESP_OK) {
            size_t hlen = snprintf((char*)part_buf, 64, _STREAM_PART, _jpg_buf_len);
            res = httpd_resp_send_chunk(req, (const char*)part_buf, hlen);
        }
        if (res == ESP_OK) {
            res = httpd_resp_send_chunk(req, (const char*)_jpg_buf, _jpg_buf_len);
        }
        if (res == ESP_OK) {
            res = httpd_resp_send_chunk(req, _STREAM_BOUNDARY, strlen(_STREAM_BOUNDARY));
        }
        if (fb) {
            esp_camera_fb_return(fb);
            fb = NULL;
            _jpg_buf = NULL;
        } 
        else if (_jpg_buf) {
            free(_jpg_buf);
            _jpg_buf = NULL;
        }
        if (res != ESP_OK) {
            break;
        }
    }
    return res;
}
 
static void startCameraServer() {
  
    httpd_config_t config = HTTPD_DEFAULT_CONFIG();
    config.server_port = 80;
    
    httpd_uri_t index_uri = {
        .uri       = "/",
        .method    = HTTP_GET,
        .handler   = stream_handler,
        .user_ctx  = NULL
    };

    if (httpd_start(&stream_httpd, &config) == ESP_OK) {
        httpd_register_uri_handler(stream_httpd, &index_uri);
    }
}
 
void setup() {

run_setup:
	
	  pinMode(4, OUTPUT);
	  digitalWrite(4, LOW);

    pinMode(33, OUTPUT);
    digitalWrite(33, LOW);
    
    WRITE_PERI_REG(RTC_CNTL_BROWN_OUT_REG, 0); // Disable brownout detector
     
    camera_config_t config;
    config.ledc_channel = LEDC_CHANNEL_0;
    config.ledc_timer = LEDC_TIMER_0;
    config.pin_d0 = Y2_GPIO_NUM;
    config.pin_d1 = Y3_GPIO_NUM;
    config.pin_d2 = Y4_GPIO_NUM;
    config.pin_d3 = Y5_GPIO_NUM;
    config.pin_d4 = Y6_GPIO_NUM;
    config.pin_d5 = Y7_GPIO_NUM;
    config.pin_d6 = Y8_GPIO_NUM;
    config.pin_d7 = Y9_GPIO_NUM;
    config.pin_xclk = XCLK_GPIO_NUM;
    config.pin_pclk = PCLK_GPIO_NUM;
    config.pin_vsync = VSYNC_GPIO_NUM;
    config.pin_href = HREF_GPIO_NUM;
    config.pin_sscb_sda = SIOD_GPIO_NUM;
    config.pin_sscb_scl = SIOC_GPIO_NUM;
    config.pin_pwdn = PWDN_GPIO_NUM;
    config.pin_reset = RESET_GPIO_NUM;
    config.xclk_freq_hz = 20000000;
    config.pixel_format = PIXFORMAT_JPEG; 
    config.frame_size = FRAMESIZE_VGA;
    config.jpeg_quality = 10;
    config.fb_count = 2;
     
    // Camera initialization
    if (esp_camera_init(&config) != ESP_OK) {
        goto run_setup;
        return;
    }

    // Cemera setup
    sensor_t* s = esp_camera_sensor_get();
    s->set_contrast(s, 2);
    s->set_brightness(s, -2);
    s->set_saturation(s, 1);
    
    // Wi-Fi connection
    for (uint32_t i = 0; WiFi.status() != WL_CONNECTED; ++i) {
        WiFi.begin(ssid, password);
        delay(1000);
    }

    // Start streaming web server
    startCameraServer();
}
 
void loop() {
    static bool is_led_enabled = false;
    static uint32_t prev_time = 0;
    if (millis() - prev_time > 500) {
        if (is_led_enabled) {
            digitalWrite(33, HIGH);
        }
        else {
            digitalWrite(33, LOW);
        }
        is_led_enabled = !is_led_enabled;
        prev_time = millis();
    }
}

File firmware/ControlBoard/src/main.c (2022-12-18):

/// ***************************************************************************
/// @file    main.c
/// @author  NeoProg
/// ***************************************************************************
#include "project-base.h"
#include "system-monitor.h"
#include "swlp.h"
#include "cli.h"
#include "servo-driver.h"
#include "motion-core.h"
#include "sensors-core.h"
#include "indication.h"
#include "display.h"
#include "pwm.h"
#include "pca9555.h"
#include "mpu6050.h"
#include "i2c1.h"
#include "i2c2.h"
#include "systimer.h"

static void system_init(void);
static void debug_gpio_init(void);
static void emergency_loop(void);



/// ***************************************************************************
/// @brief  Program entry point
/// @param  none
/// @return none
/// ***************************************************************************
void main() {
    // System initialization
    system_init();
    systimer_init();
    debug_gpio_init();
    i2c1_init(I2C1_SPEED_400KHZ);
    i2c2_init(I2C2_SPEED_400KHZ);
    
    // Modules initializaion (part 1)
    sysmon_init();
    swlp_init();
    cli_init();
    display_init();
    sensors_core_init(); // Don't change call order sensors_core_init() and indication_init()
    indication_init();
    
    // Sensors core calibration
    sensors_core_init();
    do { // Calibration loop
        if (sysmon_is_error_set(SYSMON_FATAL_ERROR)) { // Check system failure
            emergency_loop();
        }
        sysmon_process();
        indication_process();
        display_process();
    } while (sensors_core_calibration_process());
    sysmon_clear_error(SYSMON_CALIBRATION);
    
    // Motion core initialization
    servo_driver_init();
    motion_core_init();
    
    while (true) {
        // Check system failure
        if (sysmon_is_error_set(SYSMON_FATAL_ERROR)) {
            emergency_loop();
        }
        
        // Override select sequence if need
        if (sysmon_is_error_set(SYSMON_CONN_LOST)) {
            motion_core_move(NULL);
        }
        // Disable servo power if low supply voltage
        if (sysmon_is_error_set(SYSMON_VOLTAGE_ERROR)) {
            motion_core_move(NULL);
            servo_driver_power_off();
        }
        
        // Motion process
        // This 2 functions should be call in this sequence
        if (pwm_is_ready()) {
            pwm_set_lock_state(true);
            motion_core_process();
            servo_driver_process();
            pwm_set_lock_state(false);
        } else { // Here is other operations
            sysmon_process();
            swlp_process();
            indication_process();
            cli_process();
            
            if (motion_core_is_down()) {
                display_process();
            }
        }
        sensors_core_process();
    }
}

/// ***************************************************************************
/// @brief  Emergency loop
/// ***************************************************************************
static void emergency_loop(void) {
    servo_driver_power_off();
    while (true) {
        sysmon_process();
        swlp_process();
        indication_process();
        display_process();
        cli_process();
    }
}

/// ***************************************************************************
/// @brief  System initialization
/// ***************************************************************************
static void system_init(void) {
    // Enable HSE
    RCC->CR |= RCC_CR_HSEON;
    while ((RCC->CR & RCC_CR_HSERDY) != RCC_CR_HSERDY);
    
    // Configre and enable PLL
    RCC->CFGR |= RCC_CFGR_PLLSRC | (0x07 << RCC_CFGR_PLLMUL_Pos);
    RCC->CR |= RCC_CR_PLLON;
    while ((RCC->CR & RCC_CR_PLLRDY) != RCC_CR_PLLRDY);
    
    // Setup deviders for AHB(1), APB1(2), APB2(1)
    RCC->CFGR |= RCC_CFGR_HPRE_DIV1 | RCC_CFGR_PPRE1_DIV2 | RCC_CFGR_PPRE2_DIV1;
    
    // Change FLASH latency
    FLASH->ACR |= (0x02 << FLASH_ACR_LATENCY_Pos);
    
    // Switch system clocks to PLL
    RCC->CFGR |= RCC_CFGR_SW_PLL;
    while ((RCC->CFGR & RCC_CFGR_SWS_PLL) != RCC_CFGR_SWS_PLL);
    
    // Enable MCO
    RCC->CFGR |= RCC_CFGR_MCOSEL_HSI;
    
    // Switch USARTx clock source to system clock
    RCC->CFGR3 |= RCC_CFGR3_USART3SW_SYSCLK | RCC_CFGR3_USART2SW_SYSCLK | RCC_CFGR3_USART1SW_SYSCLK;
    
    
    
    // Enable GPIO clocks
    RCC->AHBENR |= RCC_AHBENR_GPIOAEN | RCC_AHBENR_GPIOBEN | RCC_AHBENR_GPIOCEN | 
                   RCC_AHBENR_GPIODEN | RCC_AHBENR_GPIOEEN | RCC_AHBENR_GPIOFEN;
    
    // Enable clocks for DMA1
    RCC->AHBENR |= RCC_AHBENR_DMA1EN;
    while ((RCC->AHBENR & RCC_AHBENR_DMA1EN) == 0);

    // Enable clocks for TIM17
    RCC->APB2ENR |= RCC_APB2ENR_TIM17EN;
    while ((RCC->APB2ENR & RCC_APB2ENR_TIM17EN) == 0); 
    DBGMCU->APB2FZ |= DBGMCU_APB2_FZ_DBG_TIM17_STOP; // Stop PWM counter for debug mode
    
    // Enable clocks for USART3
    RCC->APB1ENR |= RCC_APB1ENR_USART3EN;
    while ((RCC->APB1ENR & RCC_APB1ENR_USART3EN) == 0);

    // Enable clocks for USART2
    RCC->APB1ENR |= RCC_APB1ENR_USART2EN;
    while ((RCC->APB1ENR & RCC_APB1ENR_USART2EN) == 0);
    
    // Enable clocks for USART1
    RCC->APB2ENR |= RCC_APB2ENR_USART1EN;
    while ((RCC->APB2ENR & RCC_APB2ENR_USART1EN) == 0);
    
    // Enable clocks for I2C1
    RCC->APB1ENR |= RCC_APB1ENR_I2C1EN;
    while ((RCC->APB1ENR & RCC_APB1ENR_I2C1EN) == 0);
    
    // Enable clocks for I2C2
    RCC->APB1ENR |= RCC_APB1ENR_I2C2EN;
    while ((RCC->APB1ENR & RCC_APB1ENR_I2C2EN) == 0);
    
    // Enable clocks for ADC1 (12Mhz max)
    RCC->CFGR |= RCC_CFGR_ADCPRE_DIV6;
    RCC->APB2ENR |= RCC_APB2ENR_ADC1EN;
    while ((RCC->APB2ENR & RCC_APB2ENR_ADC1EN) == 0);
}
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

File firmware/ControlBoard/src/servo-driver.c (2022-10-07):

/// ***************************************************************************
/// @file    servo-driver.c
/// @author  NeoProg
/// ***************************************************************************
#include "project-base.h"
#include "servo-driver.h"
#include "cli.h"
#include "pwm.h"
#include "system-monitor.h"
#include "systimer.h"

#define SERVO_CONFIG_DIRECT_DIRECTION_MASK      (0x00)
#define SERVO_CONFIG_REVERSE_DIRECTION_MASK     (0x01)

#define SERVO_POWER_EN_PIN                      GPIOC, 2
#define SERVO_TURN_POWER_ON()                   gpio_set  (SERVO_POWER_EN_PIN)
#define SERVO_TURN_POWER_OFF()                  gpio_reset(SERVO_POWER_EN_PIN)

#define DS3218MG_MIN_PULSE_WIDTH                (500)
#define DS3218MG_MAX_PULSE_WIDTH                (2500)
#define DS3218MG_MAX_PHYSIC_ANGLE               (270)
#define DS3218MG_LOGIC_ZERO                     (DS3218MG_MAX_PHYSIC_ANGLE / 2)  


typedef enum {
    OVERRIDE_NO,
    OVERRIDE_LOGIC_ANGLE,
    OVERRIDE_PHYSIC_ANGLE,
    OVERRIDE_PULSE_WIDTH
} override_t;

typedef struct {
    // Runtime information
    float      logic_angle;
    float      physic_angle;
    uint16_t   pulse_width;
    override_t override_level;
    int16_t    override_value;
    
    // Configuration
    uint8_t  config;
    int16_t  zero_trim;                             
} servo_t;

CLI_CMD_HANDLER(servo_cli_cmd_help);
CLI_CMD_HANDLER(servo_cli_cmd_cfg);
CLI_CMD_HANDLER(servo_cli_cmd_power);
CLI_CMD_HANDLER(servo_cli_cmd_logging);
CLI_CMD_HANDLER(servo_cli_cmd_calibration);
CLI_CMD_HANDLER(servo_cli_cmd_set);
CLI_CMD_HANDLER(servo_cli_cmd_reset);

static const cli_cmd_t cli_cmd_list[] = {
    { .cmd = "help",        .handler = servo_cli_cmd_help        },
    { .cmd = "status",      .handler = servo_cli_cmd_cfg         },
    { .cmd = "power",       .handler = servo_cli_cmd_power       },
    { .cmd = "logging",     .handler = servo_cli_cmd_logging     },
    { .cmd = "calibration", .handler = servo_cli_cmd_calibration },
    { .cmd = "set",         .handler = servo_cli_cmd_set         },
    { .cmd = "reset",       .handler = servo_cli_cmd_reset       }
};


static servo_t servo_list[SUPPORT_SERVO_COUNT] = {0};
static bool is_enable_data_logging = false;


static void load_config(void);
static float calculate_physic_angle(float logic_angle, const servo_t* servo);


/// ***************************************************************************
/// @brief  Servo driver initialization
/// ***************************************************************************
void servo_driver_init(void) {
    // Init servo power enable pin: output mode, push-pull, high speed, no pull
    SERVO_TURN_POWER_OFF();
    gpio_set_mode        (SERVO_POWER_EN_PIN, GPIO_MODE_OUTPUT);
    gpio_set_output_type (SERVO_POWER_EN_PIN, GPIO_TYPE_PUSH_PULL);
    gpio_set_output_speed(SERVO_POWER_EN_PIN, GPIO_SPEED_LOW);
    gpio_set_pull        (SERVO_POWER_EN_PIN, GPIO_PULL_NO);
   
    load_config();
    
    pwm_init(PWM_START_FREQUENCY_HZ);
}

/// ***************************************************************************
/// @brief  Start move servo to new angle
/// @param  ch: servo channel
/// @param  angle: new angle
/// ***************************************************************************
void servo_driver_move(uint32_t ch, float angle) {
    if (ch >= SUPPORT_SERVO_COUNT) {
        sysmon_set_error(SYSMON_FATAL_ERROR);
        sysmon_disable_module(SYSMON_MODULE_SERVO_DRIVER);
        servo_driver_power_off();
        return;
    }
    servo_list[ch].logic_angle = angle;
}

/// ***************************************************************************
/// @brief  Servo driver power ON
/// *************+**************************************************************
void servo_driver_power_on(void) {
    SERVO_TURN_POWER_ON();
    pwm_set_state(true);
}

/// ***************************************************************************
/// @brief  Servo driver power OFF
/// @note   Call before system reset
/// ***************************************************************************
void servo_driver_power_off(void) {
    SERVO_TURN_POWER_OFF();
    pwm_set_state(false);
}

/// ***************************************************************************
/// @brief  Set servo speed
/// @param  speed: speed [0; 100]
/// ***************************************************************************
void servo_driver_set_speed(uint32_t speed) {
    speed = (speed > 100) ? 100 : speed;
    float factor = (float)speed / 100.0f;
    uint32_t freq = (uint32_t)(PWM_MIN_FREQUENCY_HZ + (float)(PWM_MAX_FREQUENCY_HZ - PWM_MIN_FREQUENCY_HZ) * factor);
    pwm_set_frequency(freq);
}
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

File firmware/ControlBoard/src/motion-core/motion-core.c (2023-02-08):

/// ***************************************************************************
/// @file    motion-core.c
/// @author  NeoProg
/// ***************************************************************************
#include "project-base.h"
#include "motion-core.h"
#include "motion-math.h"
#include "servo-driver.h"
#include "sensors-core.h"
#include "pwm.h"
#include "system-monitor.h"
#include "pca9555.h"
#define CHANGE_SURFACE_POS_MAX_STEP             (1.5f)

#define MOTION_MIN_STEP_HEIGHT                  (15)
#define MOTION_MAX_STEP_HEIGHT                  (60)
#define MOTION_DEFAULT_STEP_HEIGHT              (30)

#define MOTION_SURFACE_MIN_HEIGHT               (-15)
#define MOTION_SURFACE_MAX_HEIGHT               (-150)
#define MOTION_SURFACE_UP_HEIGHT_THRESHOLD      (-85)

#define MOTION_LIMBS_DOWN_TIMEOUT               (100)

#define MOTION_TIME_MIN_VALUE                   (0)
#define MOTION_TIME_MID_VALUE                   (500)
#define MOTION_TIME_MAX_VALUE                   (1000)
#define MOTION_TIME_STEP                        (20)


typedef enum {
    HEXAPOD_STATE_DOWN,
    HEXAPOD_STATE_RDY,
    HEXAPOD_STATE_MOTION_INIT,
    HEXAPOD_STATE_MOTION_EXEC,
    HEXAPOD_STATE_MOTION_DEINIT
} g_hexapod_state_t;

typedef struct {
    motion_cfg_t cfg;
    p3d_t surface_point;
    r3d_t surface_rotate;
} motion_t;


static void load_config(void);
static void main_motion_process(void);


static const v3d_t g_limbs_base_pos[] = {
    {-115, 0, 70}, {-135, 0, 0}, {-115, 0, -70}, // Left side
    { 115, 0, 70}, { 135, 0, 0}, { 115, 0, -70}  // Right side
};
static limb_t g_limbs[SUPPORT_LIMBS_COUNT] = {0};
static motion_t g_cur_motion = {0};
static ext_motion_t g_ext_motion = {0};
static g_hexapod_state_t g_hexapod_state = HEXAPOD_STATE_DOWN;
static bool g_is_surface_move_completed = false;



/// ***************************************************************************
/// @brief  Motion core initialization
/// ***************************************************************************
void motion_core_init() {
    load_config();
    
    // Load start points
    for (uint32_t i = 0; i < SUPPORT_LIMBS_COUNT; ++i) {
        g_limbs[i].pos = g_limbs_base_pos[i];
    }

    // Init motion
    g_cur_motion.surface_point.y = g_ext_motion.surface_point.y = MOTION_SURFACE_MIN_HEIGHT;
    g_cur_motion.cfg.step_height = g_ext_motion.cfg.step_height = MOTION_DEFAULT_STEP_HEIGHT;

    servo_driver_power_on();
}

/// ***************************************************************************
/// @brief  Main motion control
/// @param  ext_motion: user_motion description, may be NULL. @ref ext_motion_t
/// ***************************************************************************
void motion_core_move(const ext_motion_t* ext_motion) {
    if (!ext_motion) { 
        memset(&g_ext_motion, 0, sizeof(g_ext_motion));
        return;
    }
    g_ext_motion = *ext_motion;
    
    // Inhibit any motions if hexapod is down except change height for stand up
    if (g_hexapod_state == HEXAPOD_STATE_DOWN) {
        memset(&g_ext_motion, 0, sizeof(g_ext_motion));
        if (ext_motion->surface_point.y <= MOTION_SURFACE_UP_HEIGHT_THRESHOLD) {
            g_ext_motion.surface_point.y = ext_motion->surface_point.y;
        }
    }
}

/// ***************************************************************************
/// @brief  Get current motion parameters
/// @return Copy of motion parameters
/// ***************************************************************************
ext_motion_t motion_core_get_motion(void) {
    ext_motion_t ext_motion = {0};
    ext_motion.cfg = g_cur_motion.cfg;
    ext_motion.ctrl = g_ext_motion.ctrl;
    ext_motion.surface_point = g_cur_motion.surface_point;
    ext_motion.surface_rotate = g_cur_motion.surface_rotate;
    return ext_motion;
}

/// ***************************************************************************
/// @brief  Motion core process
/// @note   Call each PWM period from main loop
/// ***************************************************************************
extern uint16_t sensors_inputs;
void motion_core_process(void) {
    if (sysmon_is_module_disable(SYSMON_MODULE_MOTION_CORE)) return;  // Module disabled
    sysmon_clear_error(SYSMON_MATH_ERROR);
    
    //
    // Motion section
    //
    // Constrain step height before motions by hardware limits
    constrain_u16(&g_ext_motion.cfg.step_height, MOTION_MIN_STEP_HEIGHT, MOTION_MAX_STEP_HEIGHT); 
    
    // Change motion speed 
    servo_driver_set_speed(g_ext_motion.cfg.speed);

    // Motion iteration process
    main_motion_process();
    
    //
    // Make result surface
    //
    // Apply external surface
    v3d_t dst_surface_point  = g_ext_motion.surface_point;
    r3d_t dst_surface_rotate = g_ext_motion.surface_rotate;
    
    // Apply hull rotate surface
    float xz[2] = {0};
    sensors_core_get_orientation(xz);
    if (g_ext_motion.ctrl & MOTION_CTRL_EN_STAB && g_hexapod_state != HEXAPOD_STATE_DOWN) {
        dst_surface_rotate.x -= xz[0];
        dst_surface_rotate.z -= xz[1];
    }
    
    // Contrain surface rotate
    const float max_rotate_angle = 6.4f;
    constrain_float(&dst_surface_rotate.x, -max_rotate_angle, max_rotate_angle);
    constrain_float(&dst_surface_rotate.z, -max_rotate_angle, max_rotate_angle);

    // Constrain surface Y offset. Inhibit move hexapod to down while motion is progress
    float min_y_surface_point = (g_hexapod_state == HEXAPOD_STATE_MOTION_EXEC) ? MOTION_SURFACE_UP_HEIGHT_THRESHOLD : MOTION_SURFACE_MIN_HEIGHT;
    constrain_float(&dst_surface_point.y, MOTION_SURFACE_MAX_HEIGHT, min_y_surface_point);

    //
    // Move hexapod surface to destination surface
    //
    g_is_surface_move_completed = mm_move_surface(&g_cur_motion.surface_point, &dst_surface_point, &g_cur_motion.surface_rotate, &dst_surface_rotate, CHANGE_SURFACE_POS_MAX_STEP);
    
    //
    // Change hexapod state relatively reached MOTION_SURFACE_UP_HEIGHT_THRESHOLD by axis Y
    //
    if (islessequal(g_cur_motion.surface_point.y, MOTION_SURFACE_UP_HEIGHT_THRESHOLD)) { // We reach MOTION_SURFACE_UP_HEIGHT_THRESHOLD by axis Y
        if (g_is_surface_move_completed && g_hexapod_state == HEXAPOD_STATE_DOWN) {
            g_hexapod_state = HEXAPOD_STATE_RDY;
        }
    } else {
        if (g_hexapod_state == HEXAPOD_STATE_RDY) {
            g_hexapod_state = HEXAPOD_STATE_DOWN;
        }
    }

    // Calculate limbs offset relatively surface
    if (!mm_surface_calculate_offsets(g_limbs, &g_cur_motion.surface_point, &g_cur_motion.surface_rotate)) {
        sysmon_set_error(SYSMON_MATH_ERROR);
        return;
    }

    // Calculate servo logic angles
    if (!mm_kinematic_calculate_angles(g_limbs)) {
        sysmon_set_error(SYSMON_MATH_ERROR);
        return;
    }
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

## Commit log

2020-10-25 v1.00 released
    [Connectors.SchDoc, ControlBoard.PrjPcb, EEPROM map.xlsx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]
2021-08-15 v1.01 (#44)
    Release v1.01
    [BLS-5.step, Connectors.SchDoc, ControlBoard.PrjPcb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]
2022-10-07 Release 1.02-prealpha
    [Connectors.SchDoc, ControlBoard.PrjPcb, EEPROM map.xlsx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]
2025-04-08 Added calc IK step by step
    [Motion core algorithms.xlsx]
